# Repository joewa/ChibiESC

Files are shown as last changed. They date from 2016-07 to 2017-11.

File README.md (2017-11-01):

# ChibiESC

Free electric speed controller software using ChibiOS




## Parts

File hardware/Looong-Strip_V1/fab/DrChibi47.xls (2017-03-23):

Source: | /home/joerg/repos/OpenBLDC/joewa/ChibiESC/hardware/Looong-Strip_V1/DrChibi.sch
Date: | Mi 22 Mär 2017 17:17:58 CET
Tool: | Eeschema no-vcs-found-996cba7~58~ubuntu16.04.1
Generator: | /home/joerg/kicad/bom-in-python/bom_csv_grouped_by_value.py
Component Count: | 187
Individual Components:
Item | Qty | Reference(s) | Value | LibPart | Footprint | Datasheet | Comment | Manufacturer | Part Number
 |  | C1 | STM32F4:2.2u / STM32F7:4.7u | BLDC_4-rescue:C-RESCUE-BLDC_4 | Capacitors_SMD:C_0603
 |  | C2 | STM32F4:2.2u / STM32F7:0R | BLDC_4-rescue:C-RESCUE-BLDC_4 | Capacitors_SMD:C_0603
 |  | C3 | 2.2u | BLDC_4-rescue:C-RESCUE-BLDC_4 | Capacitors_SMD:C_0603
 |  | C4 | 2.2u | BLDC_4-rescue:C-RESCUE-BLDC_4 | Capacitors_SMD:C_0603
 |  | C5 | 100n | BLDC_4-rescue:C-RESCUE-BLDC_4 | Capacitors_SMD:C_0603
 |  | CDrGate1 | 0.47uF | device:C | Capacitors_SMD:C_0603_HandSoldering |  | X7R, >10V
 |  | CDrGate2 | 0.47uF | device:C | Capacitors_SMD:C_0603_HandSoldering |  | X7R, >10V
 |  | CDrGate3 | 0.47uF | device:C | Capacitors_SMD:C_0603_HandSoldering |  | X7R, >10V
 |  | CDrGate4 | 0.47uF | device:C | Capacitors_SMD:C_0603_HandSoldering |  | X7R, >10V
 |  | CDrGate5 | 0.47uF | device:C | Capacitors_SMD:C_0603_HandSoldering |  | X7R, >10V
 |  | CDrGate6 | 0.47uF | device:C | Capacitors_SMD:C_0603_HandSoldering |  | X7R, >10V
 |  | CDrHV1 | 10u,35V | device:C | Capacitors_SMD:C_1206 |  | dc link, X7R, >35V
 |  | CDrHV2 | 10u,35V | device:C | Capacitors_SMD:C_1206 |  | dc link, X7R, >35V
 |  | CDrHV3 | 10u,35V | device:C | Capacitors_SMD:C_1206 |  | dc link, X7R, >35V
 |  | CDrHV4 | 10u,35V | device:C | Capacitors_SMD:C_1206 |  | dc link, X7R, >35V
 |  | CDrHV5 | 10u,35V | device:C | Capacitors_SMD:C_1206 |  | dc link, X7R, >35V
 |  | CDrHV6 | 10u,35V | device:C | Capacitors_SMD:C_1206 |  | dc link, X7R, >35V
 |  | CDrHVX1 | C | device:C | Capacitors_SMD:C_1206
 |  | CDrHVX2 | C | device:C | Capacitors_SMD:C_1206
 |  | CDrHVX3 | C | device:C | Capacitors_SMD:C_1206
 |  | CDrHVX4 | C | device:C | Capacitors_SMD:C_1206
 |  | CDrHVX5 | C | device:C | Capacitors_SMD:C_1206
 |  | CDrHVX6 | C | device:C | Capacitors_SMD:C_1206
 |  | CDrHV1back1 | 4.7u,35V | device:C | Capacitors_SMD:C_1206 |  | dc link, X7R, >35V
 |  | CDrHV1back2 | 4.7u,35V | device:C | Capacitors_SMD:C_1206 |  | dc link, X7R, >35V
 |  | CDrHV1back3 | 4.7u,35V | device:C | Capacitors_SMD:C_1206 |  | dc link, X7R, >35V
 |  | CDrHV1back4 | 4.7u,35V | device:C | Capacitors_SMD:C_1206 |  | dc link, X7R, >35V
 |  | CDrHV1back5 | 4.7u,35V | device:C | Capacitors_SMD:C_1206 |  | dc link, X7R, >35V
 |  | CDrHV1back6 | 4.7u,35V | device:C | Capacitors_SMD:C_1206 |  | dc link, X7R, >35V
 |  | CDrHV2back1 | 10u,35V | device:C | Capacitors_SMD:C_1206_HandSoldering |  | dc link, X5R, >35V
 |  | CDrHV2back2 | 10u,35V | device:C | Capacitors_SMD:C_1206_HandSoldering |  | dc link, X5R, >35V
 |  | CDrHV2back3 | 10u,35V | device:C | Capacitors_SMD:C_1206_HandSoldering |  | dc link, X5R, >35V
 |  | CDrHV2back4 | 10u,35V | device:C | Capacitors_SMD:C_1206_HandSoldering |  | dc link, X5R, >35V
 |  | CDrHV2back5 | 10u,35V | device:C | Capacitors_SMD:C_1206_HandSoldering |  | dc link, X5R, >35V
 |  | CDrHV2back6 | 10u,35V | device:C | Capacitors_SMD:C_1206_HandSoldering |  | dc link, X5R, >35V
 |  | CDrHVs1 | 0.47u,35V | device:C | Capacitors_SMD:C_0603 |  | dc link, X7R, >35V
 |  | CDrHVs2 | 0.47u,35V | device:C | Capacitors_SMD:C_0603 |  | dc link, X7R, >35V
 |  | CDrHVs3 | 0.47u,35V | device:C | Capacitors_SMD:C_0603 |  | dc link, X7R, >35V
 |  | CDrHVs4 | 0.47u,35V | device:C | Capacitors_SMD:C_0603 |  | dc link, X7R, >35V
 |  | CDrHVs5 | 0.47u,35V | device:C | Capacitors_SMD:C_0603 |  | dc link, X7R, >35V
 |  | CDrHVs6 | 0.47u,35V | device:C | Capacitors_SMD:C_0603 |  | dc link, X7R, >35V
 |  | CDrLogic1 | 2.2uF | device:C | Capacitors_SMD:C_0603 |  | X7R, >10V | Kemet | C0603C225K8RACTU
 |  | CDrLogic2 | 2.2uF | device:C | Capacitors_SMD:C_0603 |  | X7R, >10V | Kemet | C0603C225K8RACTU
 |  | CDrLogic3 | 2.2uF | device:C | Capacitors_SMD:C_0603 |  | X7R, >10V | Kemet | C0603C225K8RACTU
 |  | CDrLogic4 | 2.2uF | device:C | Capacitors_SMD:C_0603 |  | X7R, >10V | Kemet | C0603C225K8RACTU
 |  | CDrLogic5 | 2.2uF | device:C | Capacitors_SMD:C_0603 |  | X7R, >10V | Kemet | C0603C225K8RACTU
 |  | CDrLogic6 | 2.2uF | device:C | Capacitors_SMD:C_0603 |  | X7R, >10V | Kemet | C0603C225K8RACTU
 |  | CHFAC1 | 10n,35V | device:C | Capacitors_SMD:C_0603_HandSoldering |  | Use COG or NPO ceramic. Or poly- propylene or carbonate
 |  | CONN2 | CONN_01X05 | conn:CONN_01X05 | Pads:Pin_Header_Straight_1x05_Pitch1.27mm
 |  | Cboot1 | 0.47uF | device:C | Capacitors_SMD:C_0603_HandSoldering
 |  | Cboot2 | 0.47uF | device:C | Capacitors_SMD:C_0603_HandSoldering
 |  | Cboot3 | 0.47uF | device:C | Capacitors_SMD:C_0603_HandSoldering
 |  | Cboot4 | 0.47uF | device:C | Capacitors_SMD:C_0603_HandSoldering
 |  | Cboot5 | 0.47uF | device:C | Capacitors_SMD:C_0603_HandSoldering
 |  | Cboot6 | 0.47uF | device:C | Capacitors_SMD:C_0603_HandSoldering
 |  | Ccan1 | 2.2u | BLDC_4-rescue:C-RESCUE-BLDC_4 | Capacitors_SMD:C_0603
 |  | Ccan2 | 2.2u | device:C | Capacitors_SMD:C_0603_HandSoldering
 |  | Ccfilt1 | 0.47n | device:C | Capacitors_SMD:C_0402 |  | Use COG or NPO ceramic. Or poly- propylene or carbonate
 |  | Ccfilt2 | 0.47n | device:C | Capacitors_SMD:C_0402 |  | Use COG or NPO ceramic. Or poly- propylene or carbonate
 |  | Ccfilt3 | 0.47n | device:C | Capacitors_SMD:C_0402 |  | Use COG or NPO ceramic. Or poly- propylene or carbonate
 |  | Ccfilt4 | 0.47n | device:C | Capacitors_SMD:C_0402 |  | Use COG or NPO ceramic. Or poly- propylene or carbonate
 |  | Ccfilt5 | 0.47n | device:C | Capacitors_SMD:C_0402 |  | Use COG or NPO ceramic. Or poly- propylene or carbonate
 |  | Ccfilt6 | 0.47n | device:C | Capacitors_SMD:C_0402 |  | Use COG or NPO ceramic. Or poly- propylene or carbonate
 |  | Cclk1 | 18p | BLDC_4-rescue:C-RESCUE-BLDC_4 | Capacitors_SMD:C_0402 |  | for the crystal
 |  | Cclk2 | 18p | BLDC_4-rescue:C-RESCUE-BLDC_4 | Capacitors_SMD:C_0402 |  | for the crystal
 |  | Cmcu1 | 2.2u | BLDC_4-rescue:C-RESCUE-BLDC_4 | Capacitors_SMD:C_0603
 |  | Cmcu2 | 2.2u | BLDC_4-rescue:C-RESCUE-BLDC_4 | Capacitors_SMD:C_0603
 |  | Cmcu3 | 2.2u | BLDC_4-rescue:C-RESCUE-BLDC_4 | Capacitors_SMD:C_0603
 |  | Cmcu4 | 2.2u | BLDC_4-rescue:C-RESCUE-BLDC_4 | Capacitors_SMD:C_0603
 |  | Cpwr1 | 4.7u,35V | BLDC_4-rescue:C-RESCUE-BLDC_4 | Capacitors_SMD:C_0805 |  | X7R, e.g. GRM32ER7YA106KA12L
 |  | Cpwr2 | 10u,35V | BLDC_4-rescue:C-RESCUE-BLDC_4 | Capacitors_SMD:C_2220
 |  | Csens1 | 0.47u | device:C | Capacitors_SMD:C_0603 |  | bypass capacitor for ACS711, X7R, >10V
 |  | Csens2 | 0.47u | device:C | Capacitors_SMD:C_0603 |  | bypass capacitor for ACS711, X7R, >10V
 |  | Csens3 | 0.47u | device:C | Capacitors_SMD:C_0603 |  | bypass capacitor for ACS711, X7R, >10V
 |  | Csens4 | 0.47u | device:C | Capacitors_SMD:C_0603 |  | bypass capacitor for ACS711, X7R, >10V
 |  | Csens5 | 0.47u | device:C | Capacitors_SMD:C_0603 |  | bypass capacitor for ACS711, X7R, >10V
 |  | Csens6 | 0.47u | device:C | Capacitors_SMD:C_0603 |  | bypass capacitor for ACS711, X7R, >10V
 |  | C3vi1 | 100u | BLDC_4-rescue:CP1-RESCUE-BLDC_4 | Capacitors_SMD:C_0805
 |  | C3vi2 | 1u | device:C | Capacitors_SMD:C_0603
 |  | C3vn1 | 10n | device:C | Capacitors_SMD:C_0603 |  | Use COG or NPO ceramic. Or poly- propylene or carbonate
 |  | C3vo1 | 4.7u | BLDC_4-rescue:CP1-RESCUE-BLDC_4 | Capacitors_SMD:C_0805
 |  | C5vo1 | 2.2u | BLDC_4-rescue:C-RESCUE-BLDC_4 | Capacitors_SMD:C_0603
 |  | C5vo2 | 100u | BLDC_4-rescue:CP1-RESCUE-BLDC_4 | Capacitors_SMD:C_0805
 |  | D1 | RED | BLDC_4-rescue:LED-RESCUE-BLDC_4 | LEDs:LED_0402
 |  | D2 | GREEN | BLDC_4-rescue:LED-RESCUE-BLDC_4 | LEDs:LED_0402
 |  | Dclamp1 | D_Schottky_x2_Serial_AKC__BAT754S | device:D_Schottky_x2_Serial_AKC | TO_SOT_Packages_SMD:SOT-23 |  |  | NXP | BAT754S
 |  | Dusb1 | BAT46WH | DrChibi-cache:BAT46WH | Diodes_SMD:SOD-123 |  |  | NXP | BAT46WH
 |  | JP1 | STM32F4:0R / STM32F7:DNP | device:R | Capacitors_SMD:C_0402
 |  | JP2 | STM32F4:0R / STM32F7:DNP | device:R | Capacitors_SMD:C_0402
 |  | JP3 | STM32F4:DNP / STM32F7:0R | device:R | Capacitors_SMD:C_0402
 |  | JP4 | STM32F4:0R / STM32F7:DNP | device:R | Capacitors_SMD:C_0402
 |  | JP5 | STM32F4:DNP / STM32F7:0R | device:R | Capacitors_SMD:C_0402
 |  | JP6 | STM32F4:0R / STM32F7:DNP | device:R | Capacitors_SMD:C_0402
 |  | JP8 | STM32F4:DNP / STM32F7:0R | device:R | Capacitors_SMD:C_0402
 |  | JP9 | STM32F4:0R / STM32F7:DNP | device:R | Capacitors_SMD:C_0402
 |  | JP10 | STM32F4:DNP / STM32F7:0R | device:R | Capacitors_SMD:C_0402
 |  | JP12 | STM32F4:DNP / STM32F7:0R | device:R | Capacitors_SMD:C_0402
 |  | JP13 | STM32F4:DNP / STM32F7:0R | device:R | Capacitors_SMD:C_0402
 |  | P1 | CONN_02X05 | conn:CONN_02X05 | Pads:Pin_Header_Straight_2x05_Pitch1.27mm
 |  | P3 | IN+ | DrChibi-cache:CONN_1 | Pads:1PAD_3x6mm
 |  | P4 | IN- | DrChibi-cache:CONN_1 | Pads:1PAD_3.5x6mm
 |  | P5 | CONN_01X04 | conn:CONN_01X04 | Connectors_Molex:Connector_Molex_PicoBlade_53261-0471 |  |  | Molex | PicoBlade 53261-0471
 |  | PBOOT1GND1 | PAD_SMD | pkl_misc:PAD_SMD | Pads:PAD_SMD_1x1
 |  | PBOOT0P1 | PAD_SMD | pkl_misc:PAD_SMD | Pads:PAD_SMD_1x1
 |  | PBOOT1P1 | PAD_SMD | pkl_misc:PAD_SMD | Pads:PAD_SMD_1x1
 |  | PBOOT03V31 | PAD_SMD | pkl_misc:PAD_SMD | Pads:PAD_SMD_1x1
 |  | PHFAC1 | PAD_SMD | pkl_misc:PAD_SMD | Pads:PAD_SMD_1.2x2.5
 |  | PMotor1 | PAD_SMD | pkl_misc:PAD_SMD | CRF1:1PAD_4x5mm
 |  | PMotor2 | PAD_SMD | pkl_misc:PAD_SMD | CRF1:1PAD_4x5mm
 |  | PMotor3 | PAD_SMD | pkl_misc:PAD_SMD | CRF1:1PAD_4x5mm
 |  | PMotor4 | PAD_SMD | pkl_misc:PAD_SMD | CRF1:1PAD_4x5mm
 |  | PMotor5 | PAD_SMD | pkl_misc:PAD_SMD | CRF1:1PAD_4x5mm
 |  | PMotor6 | PAD_SMD | pkl_misc:PAD_SMD | CRF1:1PAD_4x5mm
 |  | PVSens1 | PAD_SMD | pkl_misc:PAD_SMD | Pads:PAD_SMD_1x1
 |  | PVSens2 | PAD_SMD | pkl_misc:PAD_SMD | Pads:PAD_SMD_1x1
 |  | PVSens3 | PAD_SMD | pkl_misc:PAD_SMD | Pads:PAD_SMD_1x1
 |  | PVSens4 | PAD_SMD | pkl_misc:PAD_SMD | Pads:PAD_SMD_1x1
 |  | PVSens5 | PAD_SMD | pkl_misc:PAD_SMD | Pads:PAD_SMD_1x1
 |  | PVSens6 | PAD_SMD | pkl_misc:PAD_SMD | Pads:PAD_SMD_1x1
 |  | P_PWM2 | PAD_SMD | pkl_misc:PAD_SMD | Pads:PAD_SMD_1x1
 |  | P_PWM3 | PAD_SMD | pkl_misc:PAD_SMD | Pads:PAD_SMD_1x1
 |  | P_PWM4 | PAD_SMD | pkl_misc:PAD_SMD | Pads:PAD_SMD_1x1
 |  | R1 | 100R | device:R | Resistors_SMD:R_0603
 |  | R2 | 100R | device:R | Resistors_SMD:R_0603
 |  | R3 | 2k2 | device:R | Resistors_SMD:R_0402
 |  | R4 | 0R | device:R | Resistors_SMD:R_0805
 |  | RDrLogic1 | 100R | device:R | Resistors_SMD:R_0603
 |  | RDrLogic2 | 100R | device:R | Resistors_SMD:R_0603
 |  | RDrLogic3 | 100R | device:R | Resistors_SMD:R_0603
 |  | RDrLogic4 | 100R | device:R | Resistors_SMD:R_0603
 |  | RDrLogic5 | 100R | device:R | Resistors_SMD:R_0603
 |  | RDrLogic6 | 100R | device:R | Resistors_SMD:R_0603
 |  | RHFAC1 | 100R | device:R | Resistors_SMD:R_0603_HandSoldering
 |  | RY1 | R/DNP | device:R | Resistors_SMD:R_0603_HandSoldering
 |  | RY2 | R/DNP | device:R | Resistors_SMD:R_0603_HandSoldering
 |  | RY3 | R/DNP | device:R | Resistors_SMD:R_0603_HandSoldering
 |  | RY4 | R/DNP | device:R | Resistors_SMD:R_0603_HandSoldering
 |  | RY5 | R/DNP | device:R | Resistors_SMD:R_0603_HandSoldering
 |  | RY6 | R/DNP | device:R | Resistors_SMD:R_0603_HandSoldering
 |  | RYOFFS1 | 20k | device:R | Resistors_SMD:R_0603_HandSoldering
 |  | RYS1 | 0R/DNP | device:R | Resistors_SMD:R_0603_HandSoldering
 |  | RYSGND1 | 20k | device:R | Resistors_SMD:R_0402
 |  | Radj1 | 165R | device:R | Resistors_SMD:R_0402
 |  | Rcan1 | NI | BLDC_4-rescue:R-RESCUE-BLDC_4 | Resistors_SMD:R_0603_HandSoldering
 |  | Rcfilt1 | 20k | device:R | Resistors_SMD:R_0402
 |  | Rcfilt2 | 20k | device:R | Resistors_SMD:R_0402
 |  | Rcfilt3 | 20k | device:R | Resistors_SMD:R_0402
 |  | Rcfilt4 | 20k | device:R | Resistors_SMD:R_0402
 |  | Rcfilt5 | 20k | device:R | Resistors_SMD:R_0402
 |  | Rcfilt6 | 20k | device:R | Resistors_SMD:R_0402
 |  | Rhsens1 | 10k,0.1% | device:R | Capacitors_SMD:C_0603_HandSoldering
 |  | Rhsens2 | 10k,0.1% | device:R | Capacitors_SMD:C_0603_HandSoldering
 |  | Rhsens3 | 10k,0.1% | device:R | Capacitors_SMD:C_0603_HandSoldering
 |  | Rhsens4 | 10k,0.1% | device:R | Capacitors_SMD:C_0603_HandSoldering
 |  | Rhsens5 | 10k,0.1% | device:R | Capacitors_SMD:C_0603_HandSoldering
 |  | Rhsens6 | 10k,0.1% | device:R | Capacitors_SMD:C_0603_HandSoldering
 |  | Rled1 | 100R | BLDC_4-rescue:R-RESCUE-BLDC_4 | Resistors_SMD:R_0402
 |  | Rled2 | 100R | BLDC_4-rescue:R-RESCUE-BLDC_4 | Resistors_SMD:R_0402
 |  | Rlsens1 | 2k2,0.1% | device:R | Resistors_SMD:R_0402
 |  | Rlsens2 | 2k2,0.1% | device:R | Resistors_SMD:R_0402
 |  | Rlsens3 | 2k2,0.1% | device:R | Resistors_SMD:R_0402
 |  | Rlsens4 | 2k2,0.1% | device:R | Resistors_SMD:R_0402
 |  | Rlsens5 | 2k2,0.1% | device:R | Resistors_SMD:R_0402
 |  | Rlsens6 | 2k2,0.1% | device:R | Resistors_SMD:R_0402
 |  | Rthwn1 | 2k2 | device:R | Resistors_SMD:R_0402
 |  | Rusb1 | 10k | device:R | Resistors_SMD:R_0402
 |  | Rusb2 | 22R | BLDC_4-rescue:R-RESCUE-BLDC_4 | Resistors_SMD:R_0402
 |  | Rusb3 | 22R | BLDC_4-rescue:R-RESCUE-BLDC_4 | Resistors_SMD:R_0402
 |  | R3vi1 | 2R7 | device:R | Resistors_SMD:R_0805 |  | Filter resistor to Has to dissipate 1/4W.
 |  | U1 | STM32F40X_LQFP64 | crf_1:STM32F40X_LQFP64 | CRF1:lqfp64_pad_mod |  |  | ST | STM32F405RGTx
 |  | U2 | ISO1050 | crf_1:ISO1050 | CRF1:PDSO-G8
 |  | UDrmos1 | DrMOS_SiC632A | pkl_drmos:DrMOS_SiC632A | DrMOS:MLP55-31L | http://www.vishay.com/docs/62992/sic632a.pdf |  | Vishay | SiC632ACD-T1-GE3
 |  | UDrmos2 | DrMOS_SiC632A | pkl_drmos:DrMOS_SiC632A | DrMOS:MLP55-31L | http://www.vishay.com/docs/62992/sic632a.pdf |  | Vishay | SiC632ACD-T1-GE3
 |  | UDrmos3 | DrMOS_SiC632A | pkl_drmos:DrMOS_SiC632A | DrMOS:MLP55-31L | http://www.vishay.com/docs/62992/sic632a.pdf |  | Vishay | SiC632ACD-T1-GE3
 |  | UDrmos4 | DrMOS_SiC632A | pkl_drmos:DrMOS_SiC632A | DrMOS:MLP55-31L | http://www.vishay.com/docs/62992/sic632a.pdf |  | Vishay | SiC632ACD-T1-GE3
 |  | UDrmos5 | DrMOS_SiC632A | pkl_drmos:DrMOS_SiC632A | DrMOS:MLP55-31L | http://www.vishay.com/docs/62992/sic632a.pdf |  | Vishay | SiC632ACD-T1-GE3
 |  | UDrmos6 | DrMOS_SiC632A | pkl_drmos:DrMOS_SiC632A | DrMOS:MLP55-31L | http://www.vishay.com/docs/62992/sic632a.pdf |  | Vishay | SiC632ACD-T1-GE3
 |  | Ureg1 | LTM8020 | pkl_regulator:LTM8020 | Regulators_User:Housings_LGA_21_6.25x6.25mm | http://cds.linear.com/docs/en/datasheet/8020fd.pdf |  | Linear Technology | LTM8020V
 |  | Ureg2 | LP2992AIM5-3.3 | pkl_misc:LP2992AIM5-3.3 | TO_SOT_Packages_SMD:SOT-23-5 | http://www.ti.com/lit/ds/symlink/lp2992.pdf |  | Texas Instruments | LP2992AIM5-3.3/NOPB
 |  | Usens1 | ACS711 | pkl_sensor:ACS711 | Allegro:QFN-12-1EX_3x3mm_Pitch0.5mm |  |  | Allegro | ACS711KEXLT-31AB-T
 |  | Usens2 | ACS711 | pkl_sensor:ACS711 | Allegro:QFN-12-1EX_3x3mm_Pitch0.5mm |  |  | Allegro | ACS711KEXLT-31AB-T
 |  | Usens3 | ACS711 | pkl_sensor:ACS711 | Allegro:QFN-12-1EX_3x3mm_Pitch0.5mm |  |  | Allegro | ACS711KEXLT-31AB-T
 |  | Usens4 | ACS711 | pkl_sensor:ACS711 | Allegro:QFN-12-1EX_3x3mm_Pitch0.5mm |  |  | Allegro | ACS711KEXLT-31AB-T
 |  | Usens5 | ACS711 | pkl_sensor:ACS711 | Allegro:QFN-12-1EX_3x3mm_Pitch0.5mm |  |  | Allegro | ACS711KEXLT-31AB-T
 |  | Usens6 | ACS711 | pkl_sensor:ACS711 | Allegro:QFN-12-1EX_3x3mm_Pitch0.5mm |  |  | Allegro | ACS711KEXLT-31AB-T
 |  | X1 | MINI-USB-SHIELD-32005-201 | crf_1:MINI-USB-SCHIELD-32005-201 | CRF1:mini_USB_gnd |  |  | Cypress Industries | CCMUSBB-32005-201
 |  | X2 | 8MHz 10ppm | DrChibi-rescue:CRYSTAL_SMD-RESCUE-DrChibi | Crystals_User:Crystal_5x3mm |  |  |  | ABM3B-8.0-10-1UT
Collated Components:
Item | Qty | Reference(s) | Value | LibPart | Footprint | Datasheet | Comment | Manufacturer | Part Number
1 | 1 | C1 | STM32F4:2.2u / STM32F7:4.7u | BLDC_4-rescue:C-RESCUE-BLDC_4 | Capacitors_SMD:C_0603
2 | 1 | C2 | STM32F4:2.2u / STM32F7:0R | BLDC_4-rescue:C-RESCUE-BLDC_4 | Capacitors_SMD:C_0603
3 | 8 | C3, C4, Ccan1, Cmcu1, Cmcu2, Cmcu3, Cmcu4, C5vo1 | 2.2u | BLDC_4-rescue:C-RESCUE-BLDC_4 | Capacitors_SMD:C_0603
4 | 1 | C5 | 100n | BLDC_4-rescue:C-RESCUE-BLDC_4 | Capacitors_SMD:C_0603
5 | 12 | CDrGate1, CDrGate2, CDrGate3, CDrGate4, CDrGate5, CDrGate6, Cboot1, Cboot2, Cboot3, Cboot4, Cboot5, Cboot6 | 0.47uF | device:C | Capacitors_SMD:C_0603_HandSoldering |  | X7R, >10V
6 | 6 | CDrHV1, CDrHV2, CDrHV3, CDrHV4, CDrHV5, CDrHV6 | 10u,35V | device:C | Capacitors_SMD:C_1206 |  | dc link, X7R, >35V
7 | 6 | CDrHVX1, CDrHVX2, CDrHVX3, CDrHVX4, CDrHVX5, CDrHVX6 | C | device:C | Capacitors_SMD:C_1206
8 | 6 | CDrHV1back1, CDrHV1back2, CDrHV1back3, CDrHV1back4, CDrHV1back5, CDrHV1back6 | 4.7u,35V | device:C | Capacitors_SMD:C_1206 |  | dc link, X7R, >35V
9 | 6 | CDrHV2back1, CDrHV2back2, CDrHV2back3, CDrHV2back4, CDrHV2back5, CDrHV2back6 | 10u,35V | device:C | Capacitors_SMD:C_1206_HandSoldering |  | dc link, X5R, >35V
10 | 6 | CDrHVs1, CDrHVs2, CDrHVs3, CDrHVs4, CDrHVs5, CDrHVs6 | 0.47u,35V | device:C | Capacitors_SMD:C_0603 |  | dc link, X7R, >35V
11 | 6 | CDrLogic1, CDrLogic2, CDrLogic3, CDrLogic4, CDrLogic5, CDrLogic6 | 2.2uF | device:C | Capacitors_SMD:C_0603 |  | X7R, >10V | Kemet | C0603C225K8RACTU
12 | 1 | CHFAC1 | 10n,35V | device:C | Capacitors_SMD:C_0603_HandSoldering |  | Use COG or NPO ceramic. Or poly- propylene or carbonate
13 | 1 | CONN2 | CONN_01X05 | conn:CONN_01X05 | Pads:Pin_Header_Straight_1x05_Pitch1.27mm
14 | 1 | Ccan2 | 2.2u | device:C | Capacitors_SMD:C_0603_HandSoldering
15 | 6 | Ccfilt1, Ccfilt2, Ccfilt3, Ccfilt4, Ccfilt5, Ccfilt6 | 0.47n | device:C | Capacitors_SMD:C_0402 |  | Use COG or NPO ceramic. Or poly- propylene or carbonate
16 | 2 | Cclk1, Cclk2 | 18p | BLDC_4-rescue:C-RESCUE-BLDC_4 | Capacitors_SMD:C_0402 |  | for the crystal
17 | 1 | Cpwr1 | 4.7u,35V | BLDC_4-rescue:C-RESCUE-BLDC_4 | Capacitors_SMD:C_0805 |  | X7R, e.g. GRM32ER7YA106KA12L
18 | 1 | Cpwr2 | 10u,35V | BLDC_4-rescue:C-RESCUE-BLDC_4 | Capacitors_SMD:C_2220
19 | 6 | Csens1, Csens2, Csens3, Csens4, Csens5, Csens6 | 0.47u | device:C | Capacitors_SMD:C_0603 |  | bypass capacitor for ACS711, X7R, >10V
20 | 2 | C3vi1, C5vo2 | 100u | BLDC_4-rescue:CP1-RESCUE-BLDC_4 | Capacitors_SMD:C_0805
21 | 1 | C3vi2 | 1u | device:C | Capacitors_SMD:C_0603
22 | 1 | C3vn1 | 10n | device:C | Capacitors_SMD:C_0603 |  | Use COG or NPO ceramic. Or poly- propylene or carbonate
23 | 1 | C3vo1 | 4.7u | BLDC_4-rescue:CP1-RESCUE-BLDC_4 | Capacitors_SMD:C_0805
24 | 1 | D1 | RED | BLDC_4-rescue:LED-RESCUE-BLDC_4 | LEDs:LED_0402
25 | 1 | D2 | GREEN | BLDC_4-rescue:LED-RESCUE-BLDC_4 | LEDs:LED_0402
26 | 1 | Dclamp1 | D_Schottky_x2_Serial_AKC__BAT754S | device:D_Schottky_x2_Serial_AKC | TO_SOT_Packages_SMD:SOT-23 |  |  | NXP | BAT754S
27 | 1 | Dusb1 | BAT46WH | DrChibi-cache:BAT46WH | Diodes_SMD:SOD-123 |  |  | NXP | BAT46WH
28 | 5 | JP1, JP2, JP4, JP6, JP9 | STM32F4:0R / STM32F7:DNP | device:R | Capacitors_SMD:C_0402
29 | 6 | JP3, JP5, JP8, JP10, JP12, JP13 | STM32F4:DNP / STM32F7:0R | device:R | Capacitors_SMD:C_0402
30 | 1 | P1 | CONN_02X05 | conn:CONN_02X05 | Pads:Pin_Header_Straight_2x05_Pitch1.27mm
31 | 1 | P3 | IN+ | DrChibi-cache:CONN_1 | Pads:1PAD_3x6mm
32 | 1 | P4 | IN- | DrChibi-cache:CONN_1 | Pads:1PAD_3.5x6mm
33 | 1 | P5 | CONN_01X04 | conn:CONN_01X04 | Connectors_Molex:Connector_Molex_PicoBlade_53261-0471 |  |  | Molex | PicoBlade 53261-0471
34 | 13 | PBOOT1GND1, PBOOT0P1, PBOOT1P1, PBOOT03V31, PVSens1, PVSens2, PVSens3, PVSens4, PVSens5, PVSens6, P_PWM2, P_PWM3, P_PWM4 | PAD_SMD | pkl_misc:PAD_SMD | Pads:PAD_SMD_1x1
35 | 1 | PHFAC1 | PAD_SMD | pkl_misc:PAD_SMD | Pads:PAD_SMD_1.2x2.5
36 | 6 | PMotor1, PMotor2, PMotor3, PMotor4, PMotor5, PMotor6 | PAD_SMD | pkl_misc:PAD_SMD | CRF1:1PAD_4x5mm
37 | 8 | R1, R2, RDrLogic1, RDrLogic2, RDrLogic3, RDrLogic4, RDrLogic5, RDrLogic6 | 100R | device:R | Resistors_SMD:R_0603
38 | 2 | R3, Rthwn1 | 2k2 | device:R | Resistors_SMD:R_0402
39 | 1 | R4 | 0R | device:R | Resistors_SMD:R_0805
40 | 1 | RHFAC1 | 100R | device:R | Resistors_SMD:R_0603_HandSoldering
41 | 6 | RY1, RY2, RY3, RY4, RY5, RY6 | R/DNP | device:R | Resistors_SMD:R_0603_HandSoldering
42 | 1 | RYOFFS1 | 20k | device:R | Resistors_SMD:R_0603_HandSoldering
43 | 1 | RYS1 | 0R/DNP | device:R | Resistors_SMD:R_0603_HandSoldering
44 | 7 | RYSGND1, Rcfilt1, Rcfilt2, Rcfilt3, Rcfilt4, Rcfilt5, Rcfilt6 | 20k | device:R | Resistors_SMD:R_0402
45 | 1 | Radj1 | 165R | device:R | Resistors_SMD:R_0402
46 | 1 | Rcan1 | NI | BLDC_4-rescue:R-RESCUE-BLDC_4 | Resistors_SMD:R_0603_HandSoldering
47 | 6 | Rhsens1, Rhsens2, Rhsens3, Rhsens4, Rhsens5, Rhsens6 | 10k,0.1% | device:R | Capacitors_SMD:C_0603_HandSoldering
48 | 2 | Rled1, Rled2 | 100R | BLDC_4-rescue:R-RESCUE-BLDC_4 | Resistors_SMD:R_0402
49 | 6 | Rlsens1, Rlsens2, Rlsens3, Rlsens4, Rlsens5, Rlsens6 | 2k2,0.1% | device:R | Resistors_SMD:R_0402
50 | 1 | Rusb1 | 10k | device:R | Resistors_SMD:R_0402
51 | 2 | Rusb2, Rusb3 | 22R | BLDC_4-rescue:R-RESCUE-BLDC_4 | Resistors_SMD:R_0402
52 | 1 | R3vi1 | 2R7 | device:R | Resistors_SMD:R_0805 |  | Filter resistor to Has to dissipate 1/4W.
53 | 1 | U1 | STM32F40X_LQFP64 | crf_1:STM32F40X_LQFP64 | CRF1:lqfp64_pad_mod |  |  | ST | STM32F4: STM32F405RGTx / STM32F7: STM32F722RE
54 | 1 | U2 | ISO1050 | crf_1:ISO1050 | CRF1:PDSO-G8
55 | 6 | UDrmos1, UDrmos2, UDrmos3, UDrmos4, UDrmos5, UDrmos6 | DrMOS_SiC632A | pkl_drmos:DrMOS_SiC632A | DrMOS:MLP55-31L | http://www.vishay.com/docs/62992/sic632a.pdf |  | Vishay | SiC632ACD-T1-GE3
56 | 1 | Ureg1 | LTM8020 | pkl_regulator:LTM8020 | Regulators_User:Housings_LGA_21_6.25x6.25mm | http://cds.linear.com/docs/en/datasheet/8020fd.pdf |  | Linear Technology | LTM8020V
57 | 1 | Ureg2 | LP2992AIM5-3.3 | pkl_misc:LP2992AIM5-3.3 | TO_SOT_Packages_SMD:SOT-23-5 | http://www.ti.com/lit/ds/symlink/lp2992.pdf |  | Texas Instruments | LP2992AIM5-3.3/NOPB
58 | 6 | Usens1, Usens2, Usens3, Usens4, Usens5, Usens6 | ACS711 | pkl_sensor:ACS711 | Allegro:QFN-12-1EX_3x3mm_Pitch0.5mm |  |  | Allegro | ACS711KEXLT-31AB-T
59 | 1 | X1 | MINI-USB-SHIELD-32005-201 | crf_1:MINI-USB-SCHIELD-32005-201 | CRF1:mini_USB_gnd |  |  | Cypress Industries | CCMUSBB-32005-201
60 | 1 | X2 | 8MHz 10ppm | DrChibi-rescue:CRYSTAL_SMD-RESCUE-DrChibi | Crystals_User:Crystal_5x3mm |  |  |  | ABM3B-8.0-10-1UT

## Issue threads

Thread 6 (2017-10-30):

Problems with pulse pattern generation when at least two phases have the same duty cycle.

joewa, 2017-10-30:
**This test case fails:**
OK svm30.du = 0.750000000
OK svm30.dw = 0.250000000
OK svm30.dv = 0.250000000
OK svm30.mode = 1.000000000
OK pwm3dma0.enable = 1.000000000

**This test case is OK:**
OK svm30.du = 0.750000000
OK svm30.dv = 0.250000000
OK svm30.dw = 0.500000000
OK svm30.mode = 1.000000000
OK pwm3dma0.enable = 1.000000000

joewa, 2017-10-30:
This test case is OK too:
OK svm30.du = 0.250000000
OK svm30.dv = 0.250000000
OK svm30.dw = 0.750000000
OK svm30.mode = 1.000000000
OK pwm3dma0.enable = 1.000000000

The problem might occur only, when at least the last 2 phases have the same duty cycle

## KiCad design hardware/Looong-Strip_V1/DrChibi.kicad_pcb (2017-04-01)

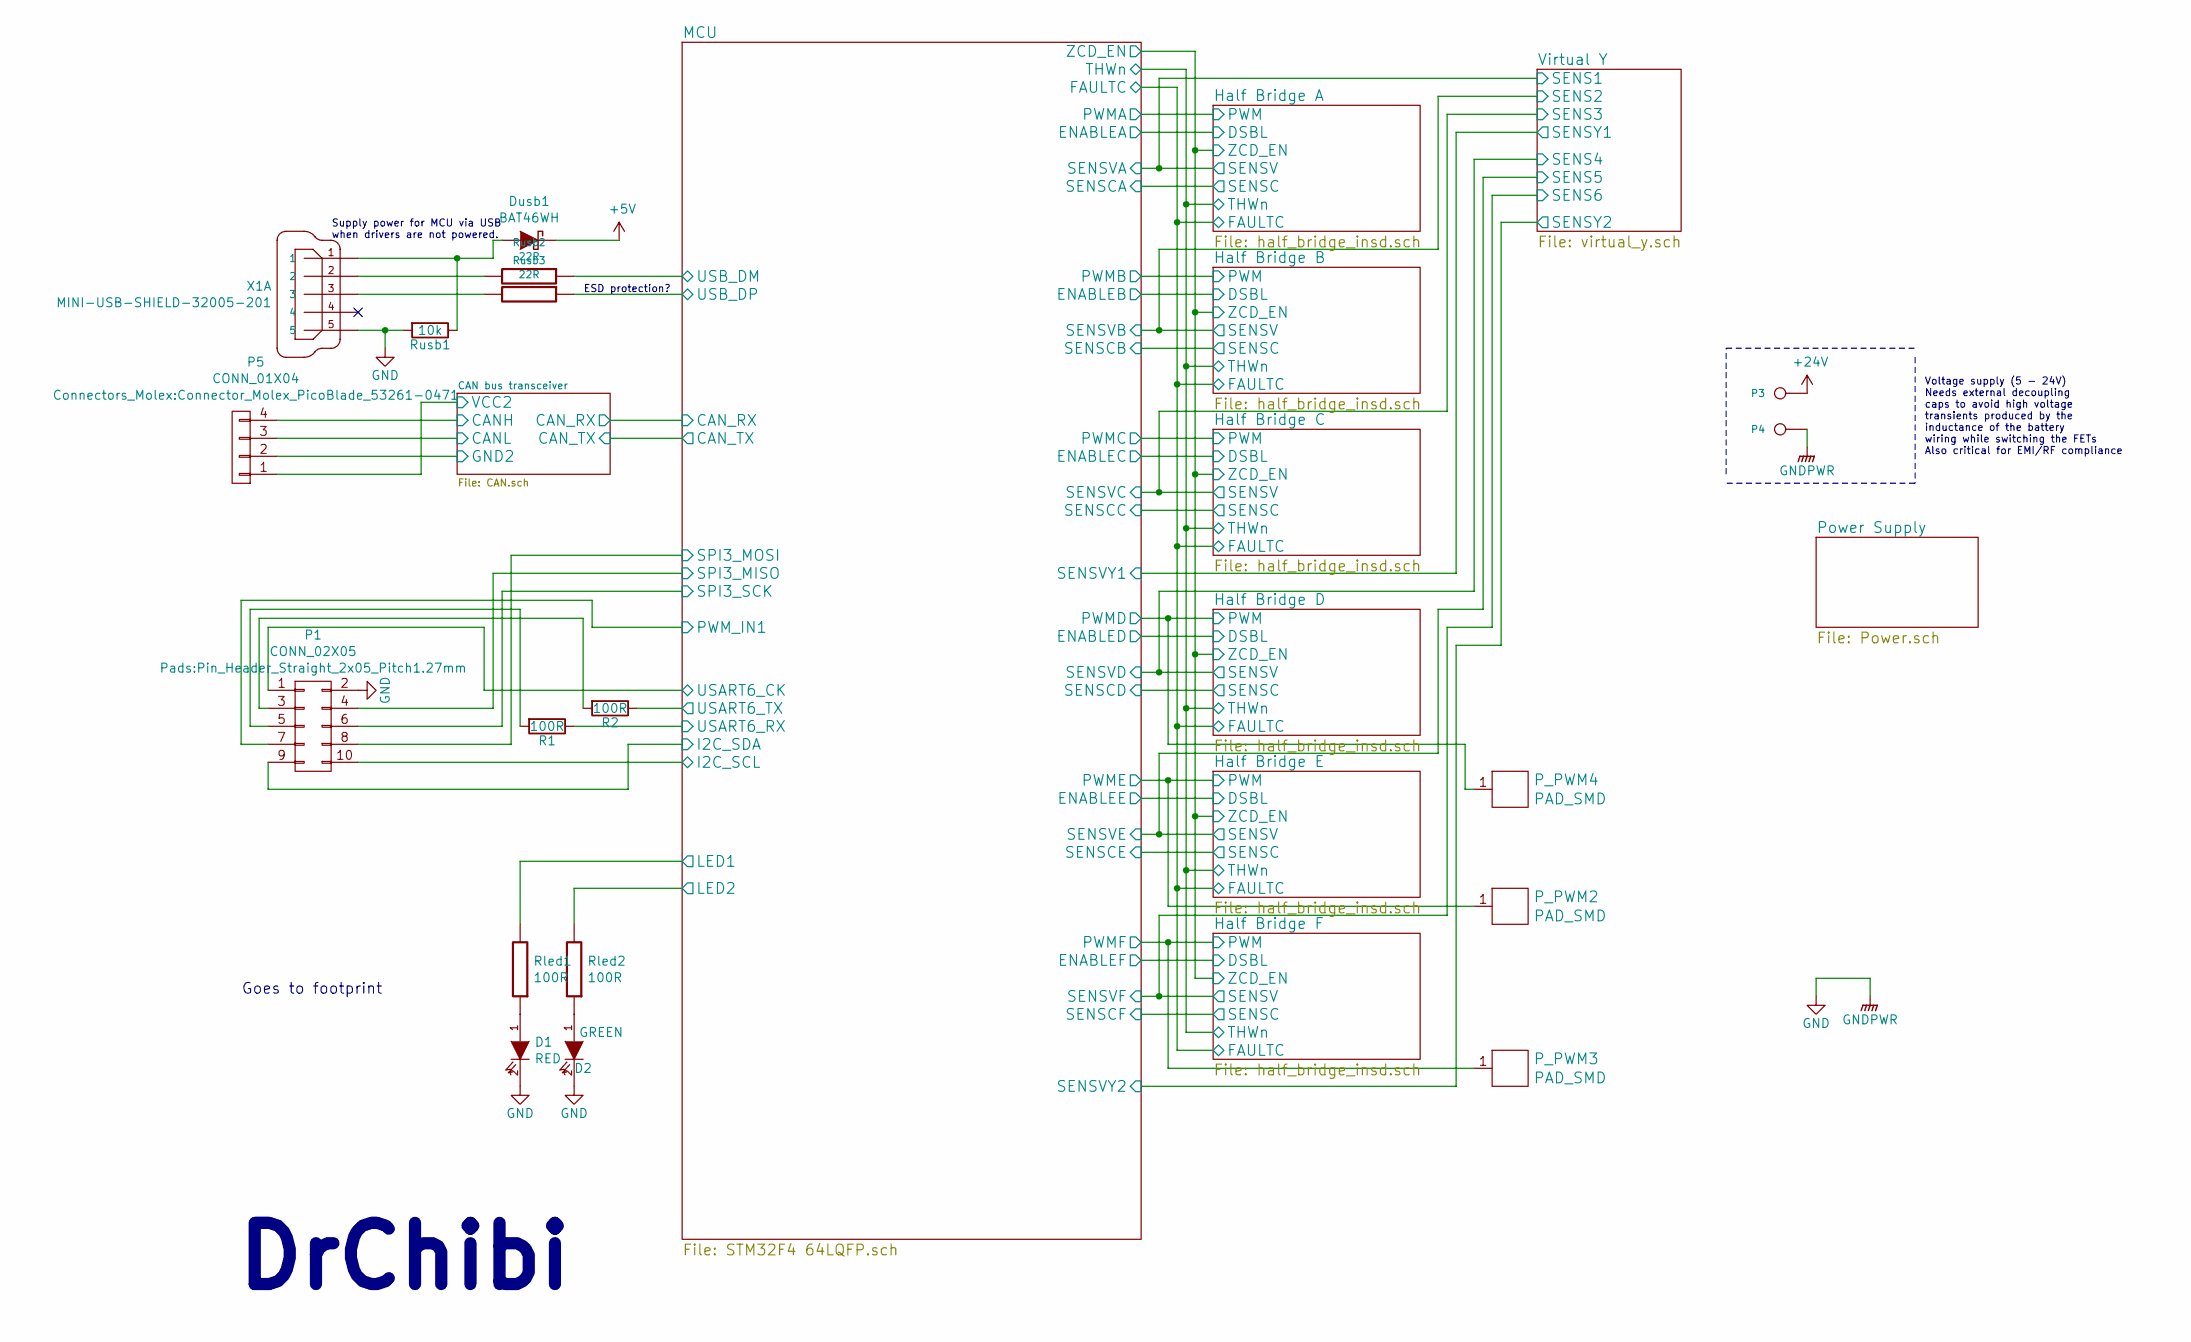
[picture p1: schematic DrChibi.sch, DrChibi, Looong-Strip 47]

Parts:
D1: RED; LED_0402
D2: GREEN; LED_0402
Dusb1: BAT46WH; SOD-123; Part Number BAT46WH
P1: CONN_02X05; Pin_Header_Straight_2x05_Pitch1.27mm
P3: IN+; 1PAD_3x6mm
P4: IN-; 1PAD_3.5x6mm
P5: CONN_01X04; Connector_Molex_PicoBlade_53261-0471; Part Number PicoBlade 53261-0471
P_PWM2, P_PWM3, P_PWM4: PAD_SMD; PAD_SMD_1x1
R1, R2: 100R; R_0603
Rled1, Rled2: 100R; R_0402
Rusb1: 10k; R_0402
Rusb2, Rusb3: 22R; R_0402
X1: MINI-USB-SHIELD-32005-201; mini_USB_gnd; Part Number CCMUSBB-32005-201

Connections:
+5V: Dusb1.1 (K); also elsewhere on the board
+24V: P3.1; also elsewhere on the board
/CAN bus transceiver/CANH: P5.4; also elsewhere on the board
/CAN bus transceiver/CANL: P5.3; also elsewhere on the board
/CAN bus transceiver/GND2: P5.2; also elsewhere on the board
/CAN bus transceiver/VCC2: P5.1; also elsewhere on the board
/Half Bridge D/PWM: P_PWM4.1; also elsewhere on the board
/Half Bridge E/PWM: P_PWM2.1; also elsewhere on the board
/Half Bridge F/PWM: P_PWM3.1; also elsewhere on the board
/MCU/I2C_SCL: P1.10; also elsewhere on the board
/MCU/I2C_SDA: P1.9; also elsewhere on the board
/MCU/LED1: Rled1.2; also elsewhere on the board
/MCU/LED2: Rled2.2; also elsewhere on the board
/MCU/PWM_IN1: P1.7; also elsewhere on the board
/MCU/SPI3_MISO: P1.4; also elsewhere on the board
/MCU/SPI3_MOSI: P1.8; also elsewhere on the board
/MCU/SPI3_SCK: P1.6; also elsewhere on the board
/MCU/USART6_CK: P1.1; also elsewhere on the board
/MCU/USART6_RX: R1.1; also elsewhere on the board
/MCU/USART6_TX: R2.1; also elsewhere on the board
/MCU/USB_DM: Rusb2.1; also elsewhere on the board
/MCU/USB_DP: Rusb3.1; also elsewhere on the board
GND: D1.2 (K), D2.2 (K), P1.2, P4.1, Rusb1.2, X1.5; also elsewhere on the board
unnamed: D1.1 (A), Rled1.1
unnamed: D2.1 (A), Rled2.1
unnamed: Dusb1.2 (A), Rusb1.1, X1.1
unnamed: P1.3, R2.2
unnamed: P1.5, R1.2
unnamed: Rusb2.2, X1.2
unnamed: Rusb3.2, X1.3

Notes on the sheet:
Supply power for MCU via USB when drivers are not powered.
ESD protection?
DrChibi
Voltage supply (5 - 24V) Needs external decoupling caps to avoid high voltage transients produced by the inductance of the battery wiring while switching the FETs Also critical for EMI/RF compliance
Goes to footprint

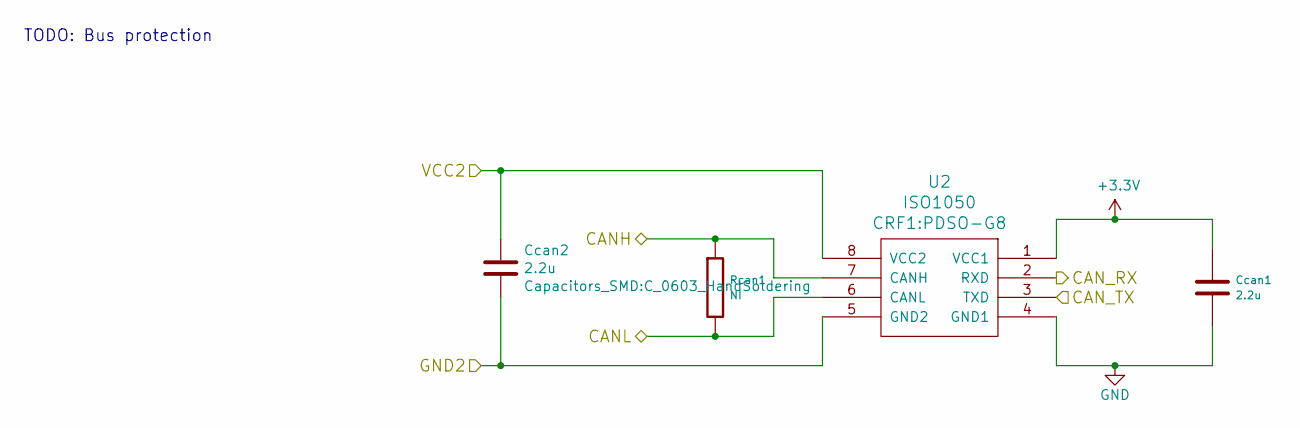
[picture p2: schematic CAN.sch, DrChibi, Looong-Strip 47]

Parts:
Ccan1: 2.2u; C_0603
Ccan2: 2.2u; C_0603_HandSoldering
Rcan1: NI; R_0603_HandSoldering
U2: ISO1050; PDSO-G8

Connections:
+3V3: Ccan1.1, U2.1 (VCC1); also elsewhere on the board
/CAN bus transceiver/CANH: Rcan1.1, U2.7 (CANH); also elsewhere on the board
/CAN bus transceiver/CANL: Rcan1.2, U2.6 (CANL); also elsewhere on the board
/CAN bus transceiver/CAN_RX: U2.2 (RXD); also elsewhere on the board
/CAN bus transceiver/CAN_TX: U2.3 (TXD); also elsewhere on the board
/CAN bus transceiver/GND2: Ccan2.2, U2.5 (GND2); also elsewhere on the board
/CAN bus transceiver/VCC2: Ccan2.1, U2.8 (VCC2); also elsewhere on the board
GND: Ccan1.2, U2.4 (GND1); also elsewhere on the board

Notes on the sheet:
TODO: Bus protection

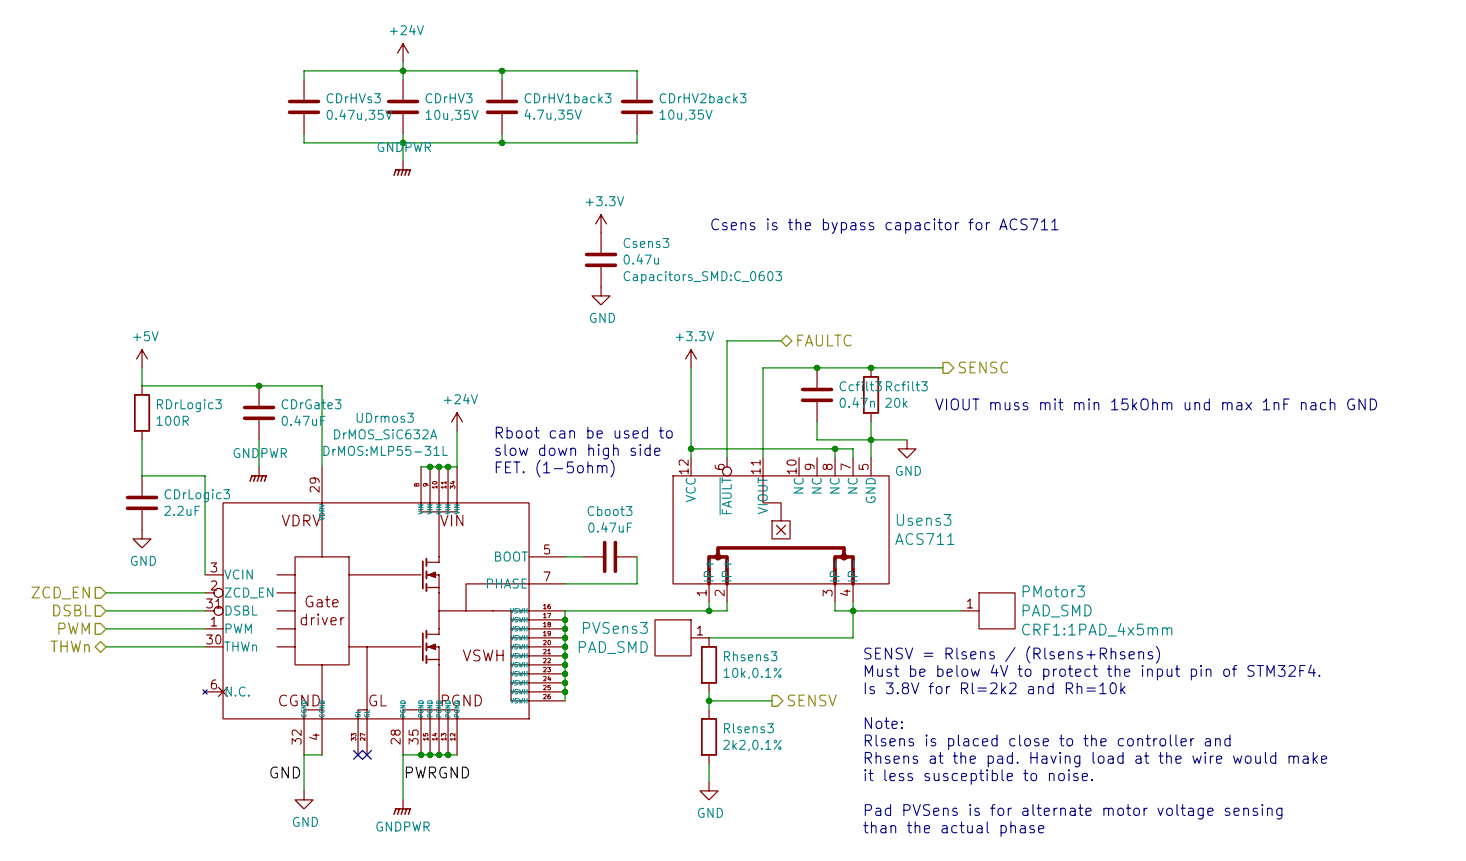
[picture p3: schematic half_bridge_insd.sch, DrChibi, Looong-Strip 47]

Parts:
CDrGate1: 0.47uF; C_0603_HandSoldering
CDrHV1: 10u,35V; C_1206
CDrHV1back1: 4.7u,35V; C_1206
CDrHV2back1: 10u,35V; C_1206_HandSoldering
CDrHVs1: 0.47u,35V; C_0603
CDrLogic1: 2.2uF; C_0603; Part Number C0603C225K8RACTU
Cboot1: 0.47uF; C_0603_HandSoldering
Ccfilt1: 0.47n; C_0402
Csens1: 0.47u; C_0603
PMotor1: PAD_SMD; 1PAD_4x5mm
PVSens1: PAD_SMD; PAD_SMD_1x1
RDrLogic1: 100R; R_0603
Rcfilt1: 20k; R_0402
Rhsens1: 10k,0.1%; C_0603_HandSoldering
Rlsens1: 2k2,0.1%; R_0402
UDrmos1: DrMOS_SiC632A; MLP55-31L; Part Number SiC632ACD-T1-GE3
Usens1: ACS711; QFN-12-1EX_3x3mm_Pitch0.5mm; Part Number ACS711KEXLT-31AB-T

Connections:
+3V3: Csens1.1, Usens1.7 (NC), Usens1.8 (NC), Usens1.12 (VCC); also elsewhere on the board
+5V: CDrGate1.1, RDrLogic1.1, UDrmos1.29 (VDRV); also elsewhere on the board
+24V: CDrHV1.1, CDrHV1back1.1, CDrHV2back1.1, CDrHVs1.1, UDrmos1.8 (VIN), UDrmos1.9 (VIN), UDrmos1.10 (VIN), UDrmos1.11 (VIN), UDrmos1.34 (VIN); also elsewhere on the board
/Half Bridge A/DSBL: UDrmos1.31 (DSBL); also elsewhere on the board
/Half Bridge A/FAULTC: Usens1.6 (~FAULT); also elsewhere on the board
/Half Bridge A/PWM: UDrmos1.1 (PWM); also elsewhere on the board
/Half Bridge A/SENSC: Ccfilt1.1, Rcfilt1.1, Usens1.11 (VIOUT); also elsewhere on the board
/Half Bridge A/THWn: UDrmos1.30 (THWn); also elsewhere on the board
/Half Bridge A/ZCD_EN: UDrmos1.2 (ZCD_EN); also elsewhere on the board
/Virtual Y/SENS1: Rhsens1.2, Rlsens1.1; also elsewhere on the board
GND: CDrGate1.2, CDrHV1.2, CDrHV1back1.2, CDrHV2back1.2, CDrHVs1.2, CDrLogic1.2, Ccfilt1.2, Csens1.2, Rcfilt1.2, Rlsens1.2, UDrmos1.4 (CGND), UDrmos1.12 (PGND), UDrmos1.13 (PGND), UDrmos1.14 (PGND), UDrmos1.15 (PGND), UDrmos1.28 (PGND), UDrmos1.32 (CGND), UDrmos1.35 (PGND), Usens1.5 (GND); also elsewhere on the board
unnamed: CDrLogic1.1, RDrLogic1.2, UDrmos1.3 (VCIN)
unnamed: Cboot1.1, UDrmos1.7 (PHASE)
unnamed: Cboot1.2, UDrmos1.5 (BOOT)
unnamed: PMotor1.1, PVSens1.1, Rhsens1.1, Usens1.3 (IP-), Usens1.4 (IP-)
unnamed: UDrmos1.16 (VSWH), UDrmos1.17 (VSWH), UDrmos1.18 (VSWH), UDrmos1.19 (VSWH), UDrmos1.20 (VSWH), UDrmos1.21 (VSWH), UDrmos1.22 (VSWH), UDrmos1.23 (VSWH), UDrmos1.24 (VSWH), UDrmos1.25 (VSWH), UDrmos1.26 (VSWH), Usens1.1 (IP+), Usens1.2 (IP+)

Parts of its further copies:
C20, C21, C22, C23: 0.47uF; C_0603_HandSoldering
CDrGate2, CDrGate3, CDrGate4, CDrGate5, CDrGate6: 0.47uF; C_0603_HandSoldering
CDrHV1back2, CDrHV1back3, CDrHV1back4, CDrHV1back5, CDrHV1back6: 4.7u,35V; C_1206
CDrHV2, CDrHV3, CDrHV4, CDrHV5, CDrHV6: 10u,35V; C_1206
CDrHV2back2, CDrHV2back3, CDrHV2back4, CDrHV2back5, CDrHV2back6: 10u,35V; C_1206_HandSoldering
CDrHVs2, CDrHVs3, CDrHVs4, CDrHVs5, CDrHVs6: 0.47u,35V; C_0603
CDrLogic2, CDrLogic3, CDrLogic4, CDrLogic5, CDrLogic6: 2.2uF; C_0603; Part Number C0603C225K8RACTU
Cboot2, Cboot3, Cboot4, Cboot5, Cboot6: 0.47uF; C_0603_HandSoldering
Ccfilt2, Ccfilt3, Ccfilt4, Ccfilt5, Ccfilt6: 0.47n; C_0402
Csens2, Csens3, Csens4, Csens5, Csens6: 0.47u; C_0603
PMotor2, PMotor3, PMotor4, PMotor5, PMotor6: PAD_SMD; 1PAD_4x5mm
PVSens2, PVSens3, PVSens4, PVSens5, PVSens6: PAD_SMD; PAD_SMD_1x1
RDrLogic2, RDrLogic3, RDrLogic4, RDrLogic5, RDrLogic6: 100R; R_0603
Rcfilt2, Rcfilt3, Rcfilt4, Rcfilt5, Rcfilt6: 20k; R_0402
Rhsens2, Rhsens3, Rhsens4, Rhsens5, Rhsens6: 10k,0.1%; C_0603_HandSoldering
Rlsens2, Rlsens3, Rlsens4, Rlsens5, Rlsens6: 2k2,0.1%; R_0402
UDrmos2, UDrmos3, UDrmos4, UDrmos5, UDrmos6: DrMOS_SiC632A; MLP55-31L; Part Number SiC632ACD-T1-GE3
Usens2, Usens3, Usens4, Usens5, Usens6: ACS711; QFN-12-1EX_3x3mm_Pitch0.5mm; Part Number ACS711KEXLT-31AB-T

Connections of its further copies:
+3V3: Csens2.1, Csens3.1, Csens4.1, Csens5.1, Csens6.1, Usens2.7 (NC), Usens2.8 (NC), Usens2.12 (VCC), Usens3.7 (NC), Usens3.8 (NC), Usens3.12 (VCC), Usens4.7 (NC), Usens4.8 (NC), Usens4.12 (VCC), Usens5.7 (NC), Usens5.8 (NC), Usens5.12 (VCC), Usens6.7 (NC), Usens6.8 (NC), Usens6.12 (VCC); also elsewhere on the board
+5V: CDrGate2.1, CDrGate3.1, CDrGate4.1, CDrGate5.1, CDrGate6.1, RDrLogic2.1, RDrLogic3.1, RDrLogic4.1, RDrLogic5.1, RDrLogic6.1, UDrmos2.29 (VDRV), UDrmos3.29 (VDRV), UDrmos4.29 (VDRV), UDrmos5.29 (VDRV), UDrmos6.29 (VDRV); also elsewhere on the board
+24V: CDrHV1back2.1, CDrHV1back3.1, CDrHV1back4.1, CDrHV1back5.1, CDrHV1back6.1, CDrHV2.1, CDrHV2back2.1, CDrHV2back3.1, CDrHV2back4.1, CDrHV2back5.1, CDrHV2back6.1, CDrHV3.1, CDrHV4.1, CDrHV5.1, CDrHV6.1, CDrHVs2.1, CDrHVs3.1, CDrHVs4.1, CDrHVs5.1, CDrHVs6.1, UDrmos2.8 (VIN), UDrmos2.9 (VIN), UDrmos2.10 (VIN), UDrmos2.11 (VIN), UDrmos2.34 (VIN), UDrmos3.8 (VIN), UDrmos3.9 (VIN), UDrmos3.10 (VIN), UDrmos3.11 (VIN), UDrmos3.34 (VIN), UDrmos4.8 (VIN), UDrmos4.9 (VIN), UDrmos4.10 (VIN), UDrmos4.11 (VIN), UDrmos4.34 (VIN), UDrmos5.8 (VIN), UDrmos5.9 (VIN), UDrmos5.10 (VIN), UDrmos5.11 (VIN), UDrmos5.34 (VIN), UDrmos6.8 (VIN), UDrmos6.9 (VIN), UDrmos6.10 (VIN), UDrmos6.11 (VIN), UDrmos6.34 (VIN); also elsewhere on the board
/Half Bridge A/FAULTC: Usens2.6 (~FAULT), Usens3.6 (~FAULT), Usens4.6 (~FAULT), Usens5.6 (~FAULT), Usens6.6 (~FAULT); also elsewhere on the board
/Half Bridge A/THWn: UDrmos2.30 (THWn), UDrmos3.30 (THWn), UDrmos4.30 (THWn), UDrmos5.30 (THWn), UDrmos6.30 (THWn); also elsewhere on the board
/Half Bridge A/ZCD_EN: UDrmos2.2 (ZCD_EN), UDrmos3.2 (ZCD_EN), UDrmos4.2 (ZCD_EN), UDrmos5.2 (ZCD_EN), UDrmos6.2 (ZCD_EN); also elsewhere on the board
/Half Bridge B/DSBL: UDrmos2.31 (DSBL); also elsewhere on the board
/Half Bridge B/PWM: UDrmos2.1 (PWM); also elsewhere on the board
/Half Bridge B/SENSC: Ccfilt2.1, Rcfilt2.1, Usens2.11 (VIOUT); also elsewhere on the board
/Half Bridge C/DSBL: UDrmos3.31 (DSBL); also elsewhere on the board
/Half Bridge C/PWM: UDrmos3.1 (PWM); also elsewhere on the board
/Half Bridge C/SENSC: Ccfilt3.1, Rcfilt3.1, Usens3.11 (VIOUT); also elsewhere on the board
/Half Bridge D/DSBL: UDrmos4.31 (DSBL); also elsewhere on the board
/Half Bridge D/PWM: UDrmos4.1 (PWM); also elsewhere on the board
/Half Bridge D/SENSC: Ccfilt4.1, Rcfilt4.1, Usens4.11 (VIOUT); also elsewhere on the board
/Half Bridge E/DSBL: UDrmos5.31 (DSBL); also elsewhere on the board
/Half Bridge E/PWM: UDrmos5.1 (PWM); also elsewhere on the board
/Half Bridge E/SENSC: Ccfilt5.1, Rcfilt5.1, Usens5.11 (VIOUT); also elsewhere on the board
/Half Bridge F/DSBL: UDrmos6.31 (DSBL); also elsewhere on the board
/Half Bridge F/PWM: UDrmos6.1 (PWM); also elsewhere on the board
/Half Bridge F/SENSC: Ccfilt6.1, Rcfilt6.1, Usens6.11 (VIOUT); also elsewhere on the board
/Virtual Y/SENS2: Rhsens2.2, Rlsens2.1; also elsewhere on the board
/Virtual Y/SENS3: Rhsens3.2, Rlsens3.1; also elsewhere on the board
/Virtual Y/SENS4: Rhsens4.2, Rlsens4.1; also elsewhere on the board
/Virtual Y/SENS5: Rhsens5.2, Rlsens5.1; also elsewhere on the board
/Virtual Y/SENS6: Rhsens6.2, Rlsens6.1; also elsewhere on the board
GND: CDrGate2.2, CDrGate3.2, CDrGate4.2, CDrGate5.2, CDrGate6.2, CDrHV1back2.2, CDrHV1back3.2, CDrHV1back4.2, CDrHV1back5.2, CDrHV1back6.2, CDrHV2.2, CDrHV2back2.2, CDrHV2back3.2, CDrHV2back4.2, CDrHV2back5.2, CDrHV2back6.2, CDrHV3.2, CDrHV4.2, CDrHV5.2, CDrHV6.2, CDrHVs2.2, CDrHVs3.2, CDrHVs4.2, CDrHVs5.2, CDrHVs6.2, CDrLogic2.2, CDrLogic3.2, CDrLogic4.2, CDrLogic5.2, CDrLogic6.2, Ccfilt2.2, Ccfilt3.2, Ccfilt4.2, Ccfilt5.2, Ccfilt6.2, Csens2.2, Csens3.2, Csens4.2, Csens5.2, Csens6.2, Rcfilt2.2, Rcfilt3.2, Rcfilt4.2, Rcfilt5.2, Rcfilt6.2, Rlsens2.2, Rlsens3.2, Rlsens4.2, Rlsens5.2, Rlsens6.2, UDrmos2.4 (CGND), UDrmos2.12 (PGND), UDrmos2.13 (PGND), UDrmos2.14 (PGND), UDrmos2.15 (PGND), UDrmos2.28 (PGND), UDrmos2.32 (CGND), UDrmos2.35 (PGND), UDrmos3.4 (CGND), UDrmos3.12 (PGND), UDrmos3.13 (PGND), UDrmos3.14 (PGND), UDrmos3.15 (PGND), UDrmos3.28 (PGND), UDrmos3.32 (CGND), UDrmos3.35 (PGND), UDrmos4.4 (CGND), UDrmos4.12 (PGND), UDrmos4.13 (PGND), UDrmos4.14 (PGND), UDrmos4.15 (PGND), UDrmos4.28 (PGND), UDrmos4.32 (CGND), UDrmos4.35 (PGND), UDrmos5.4 (CGND), UDrmos5.12 (PGND), UDrmos5.13 (PGND), UDrmos5.14 (PGND), UDrmos5.15 (PGND), UDrmos5.28 (PGND), UDrmos5.32 (CGND), UDrmos5.35 (PGND), UDrmos6.4 (CGND), UDrmos6.12 (PGND), UDrmos6.13 (PGND), UDrmos6.14 (PGND), UDrmos6.15 (PGND), UDrmos6.28 (PGND), UDrmos6.32 (CGND), UDrmos6.35 (PGND), Usens2.5 (GND), Usens3.5 (GND), Usens4.5 (GND), Usens5.5 (GND), Usens6.5 (GND); also elsewhere on the board
unnamed: CDrLogic2.1, RDrLogic2.2, UDrmos2.3 (VCIN)
unnamed: CDrLogic3.1, RDrLogic3.2, UDrmos3.3 (VCIN)
unnamed: CDrLogic4.1, RDrLogic4.2, UDrmos4.3 (VCIN)
unnamed: CDrLogic5.1, RDrLogic5.2, UDrmos5.3 (VCIN)
unnamed: CDrLogic6.1, RDrLogic6.2, UDrmos6.3 (VCIN)
unnamed: Cboot2.1, UDrmos2.7 (PHASE)
unnamed: Cboot2.2, UDrmos2.5 (BOOT)
unnamed: Cboot3.1, UDrmos3.7 (PHASE)
unnamed: Cboot3.2, UDrmos3.5 (BOOT)
unnamed: Cboot4.1, UDrmos4.7 (PHASE)
unnamed: Cboot4.2, UDrmos4.5 (BOOT)
unnamed: Cboot5.1, UDrmos5.7 (PHASE)
unnamed: Cboot5.2, UDrmos5.5 (BOOT)
unnamed: Cboot6.1, UDrmos6.7 (PHASE)
unnamed: Cboot6.2, UDrmos6.5 (BOOT)
unnamed: PMotor2.1, PVSens2.1, Rhsens2.1, Usens2.3 (IP-), Usens2.4 (IP-)
unnamed: PMotor3.1, PVSens3.1, Rhsens3.1, Usens3.3 (IP-), Usens3.4 (IP-)
unnamed: PMotor4.1, PVSens4.1, Rhsens4.1, Usens4.3 (IP-), Usens4.4 (IP-)
unnamed: PMotor5.1, PVSens5.1, Rhsens5.1, Usens5.3 (IP-), Usens5.4 (IP-)
unnamed: PMotor6.1, PVSens6.1, Rhsens6.1, Usens6.3 (IP-), Usens6.4 (IP-)
unnamed: UDrmos2.16 (VSWH), UDrmos2.17 (VSWH), UDrmos2.18 (VSWH), UDrmos2.19 (VSWH), UDrmos2.20 (VSWH), UDrmos2.21 (VSWH), UDrmos2.22 (VSWH), UDrmos2.23 (VSWH), UDrmos2.24 (VSWH), UDrmos2.25 (VSWH), UDrmos2.26 (VSWH), Usens2.1 (IP+), Usens2.2 (IP+)
unnamed: UDrmos3.16 (VSWH), UDrmos3.17 (VSWH), UDrmos3.18 (VSWH), UDrmos3.19 (VSWH), UDrmos3.20 (VSWH), UDrmos3.21 (VSWH), UDrmos3.22 (VSWH), UDrmos3.23 (VSWH), UDrmos3.24 (VSWH), UDrmos3.25 (VSWH), UDrmos3.26 (VSWH), Usens3.1 (IP+), Usens3.2 (IP+)
unnamed: UDrmos4.16 (VSWH), UDrmos4.17 (VSWH), UDrmos4.18 (VSWH), UDrmos4.19 (VSWH), UDrmos4.20 (VSWH), UDrmos4.21 (VSWH), UDrmos4.22 (VSWH), UDrmos4.23 (VSWH), UDrmos4.24 (VSWH), UDrmos4.25 (VSWH), UDrmos4.26 (VSWH), Usens4.1 (IP+), Usens4.2 (IP+)
unnamed: UDrmos5.16 (VSWH), UDrmos5.17 (VSWH), UDrmos5.18 (VSWH), UDrmos5.19 (VSWH), UDrmos5.20 (VSWH), UDrmos5.21 (VSWH), UDrmos5.22 (VSWH), UDrmos5.23 (VSWH), UDrmos5.24 (VSWH), UDrmos5.25 (VSWH), UDrmos5.26 (VSWH), Usens5.1 (IP+), Usens5.2 (IP+)
unnamed: UDrmos6.16 (VSWH), UDrmos6.17 (VSWH), UDrmos6.18 (VSWH), UDrmos6.19 (VSWH), UDrmos6.20 (VSWH), UDrmos6.21 (VSWH), UDrmos6.22 (VSWH), UDrmos6.23 (VSWH), UDrmos6.24 (VSWH), UDrmos6.25 (VSWH), UDrmos6.26 (VSWH), Usens6.1 (IP+), Usens6.2 (IP+)

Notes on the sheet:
VIOUT muss mit min 15kOhm und max 1nF nach GND
Rboot can be used to slow down high side FET. (1-5ohm)
SENSV = Rlsens / (Rlsens+Rhsens) Must be below 4V to protect the input pin of STM32F4. Is 3.8V for Rl=2k2 and Rh=10k Note: Rlsens is placed close to the controller and Rhsens at the pad. Having load at the wire would make it less susceptible to noise. Pad PVSens is for alternate motor voltage sensi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
Csens is the bypass capacitor for ACS711

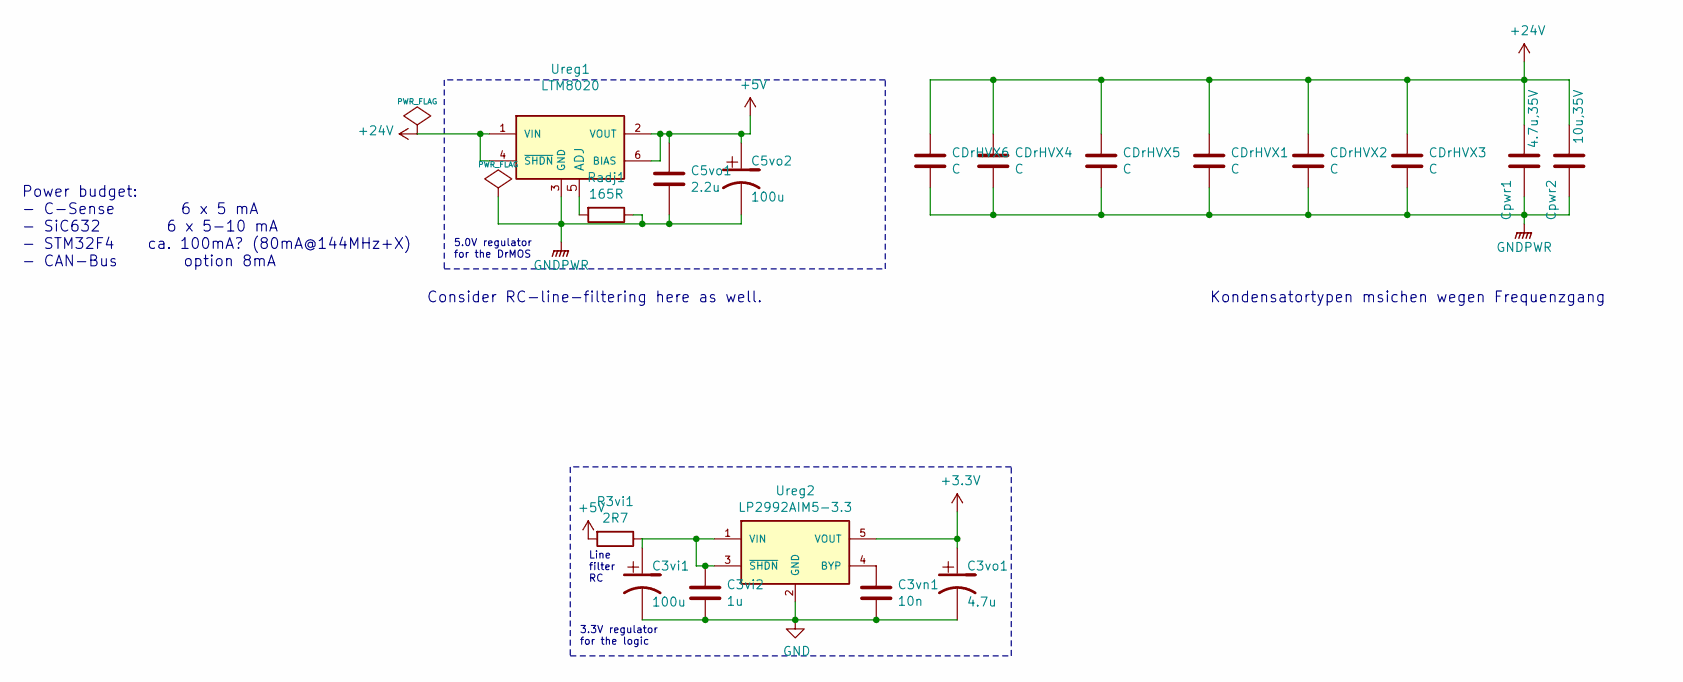
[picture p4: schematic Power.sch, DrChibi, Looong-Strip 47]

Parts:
C3vi1, C5vo2: 100u; C_0805
C3vi2: 1u; C_0603
C3vn1: 10n; C_0603
C3vo1: 4.7u; C_0805
C5vo1: 2.2u; C_0603
CDrHVX1, CDrHVX2, CDrHVX3, CDrHVX4, CDrHVX5, CDrHVX6: C; C_1206
Cpwr1: 4.7u,35V; C_0805
Cpwr2: 10u,35V; C_2220
R3vi1: 2R7; R_0805
Radj1: 165R; R_0402
Ureg1: LTM8020; Housings_LGA_21_6.25x6.25mm; Part Number LTM8020V
Ureg2: LP2992AIM5-3.3; SOT-23-5; Part Number LP2992AIM5-3.3/NOPB

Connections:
+3V3: C3vo1.1, Ureg2.5 (VOUT); also elsewhere on the board
+5V: C5vo1.1, C5vo2.1, R3vi1.2, Ureg1.2 (VOUT), Ureg1.6 (BIAS); also elsewhere on the board
+24V: CDrHVX1.1, CDrHVX2.1, CDrHVX3.1, CDrHVX4.1, CDrHVX5.1, CDrHVX6.1, Cpwr1.2, Cpwr2.2, Ureg1.1 (VIN), Ureg1.4 (~SHDN~); also elsewhere on the board
GND: C3vi1.2, C3vi2.2, C3vn1.2, C3vo1.2, C5vo1.2, C5vo2.2, CDrHVX1.2, CDrHVX2.2, CDrHVX3.2, CDrHVX4.2, CDrHVX5.2, CDrHVX6.2, Cpwr1.1, Cpwr2.1, Radj1.1, Ureg1.3 (GND), Ureg2.2 (GND); also elsewhere on the board
unnamed: C3vi1.1, C3vi2.1, R3vi1.1, Ureg2.1 (VIN), Ureg2.3 (~SHDN~)
unnamed: C3vn1.1, Ureg2.4 (BYP)
unnamed: Radj1.2, Ureg1.5 (ADJ)

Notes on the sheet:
5.0V regulator for the DrMOS
3.3V regulator for the logic
Kondensatortypen msichen wegen Frequenzgang
Line filter RC
Consider RC-line-filtering here as well.
Power budget: - C-Sense 6 x 5 mA - SiC632 6 x 5-10 mA - STM32F4 ca. 100mA? (80mA@144MHz+X) - CAN-Bus option 8mA

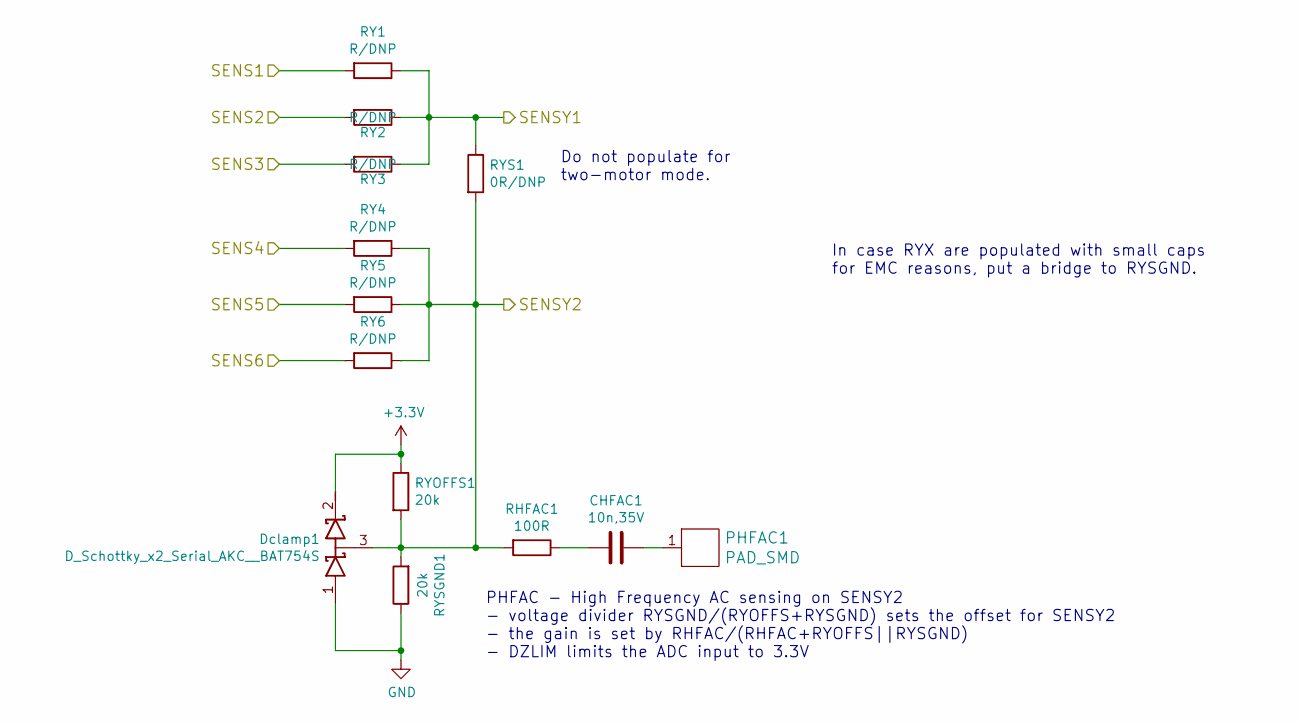
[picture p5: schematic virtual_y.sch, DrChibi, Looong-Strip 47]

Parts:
CHFAC1: 10n,35V; C_0603_HandSoldering
Dclamp1: D_Schottky_x2_Serial_AKC__BAT754S; SOT-23; Part Number BAT754S
PHFAC1: PAD_SMD; PAD_SMD_1.2x2.5
RHFAC1: 100R; R_0603_HandSoldering
RY1, RY2, RY3, RY4, RY5, RY6: R/DNP; R_0603_HandSoldering
RYOFFS1: 20k; R_0603_HandSoldering
RYS1: 0R/DNP; R_0603_HandSoldering
RYSGND1: 20k; R_0402

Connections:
+3V3: Dclamp1.2 (K), RYOFFS1.1; also elsewhere on the board
/MCU/SENSVY1: RY1.1, RY2.1, RY3.1, RYS1.1; also elsewhere on the board
/MCU/SENSVY2: Dclamp1.3 (common), RHFAC1.2, RY4.1, RY5.1, RY6.1, RYOFFS1.2, RYS1.2, RYSGND1.2; also elsewhere on the board
/Virtual Y/SENS1: RY1.2; also elsewhere on the board
/Virtual Y/SENS2: RY2.2; also elsewhere on the board
/Virtual Y/SENS3: RY3.2; also elsewhere on the board
/Virtual Y/SENS4: RY4.2; also elsewhere on the board
/Virtual Y/SENS5: RY5.2; also elsewhere on the board
/Virtual Y/SENS6: RY6.2; also elsewhere on the board
GND: Dclamp1.1 (A), RYSGND1.1; also elsewhere on the board
unnamed: CHFAC1.1, PHFAC1.1
unnamed: CHFAC1.2, RHFAC1.1

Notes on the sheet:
Do not populate for two-motor mode.
In case RYX are populated with small caps for EMC reasons, put a bridge to RYSGND.
PHFAC - High Frequency AC sensing on SENSY2 - voltage divider RYSGND/(RYOFFS+RYSGND) sets the offset for SENSY2 - the gain is set by RHFAC/(RHFAC+RYOFFS||RYSGND) - DZLIM limits the ADC input to 3.3V

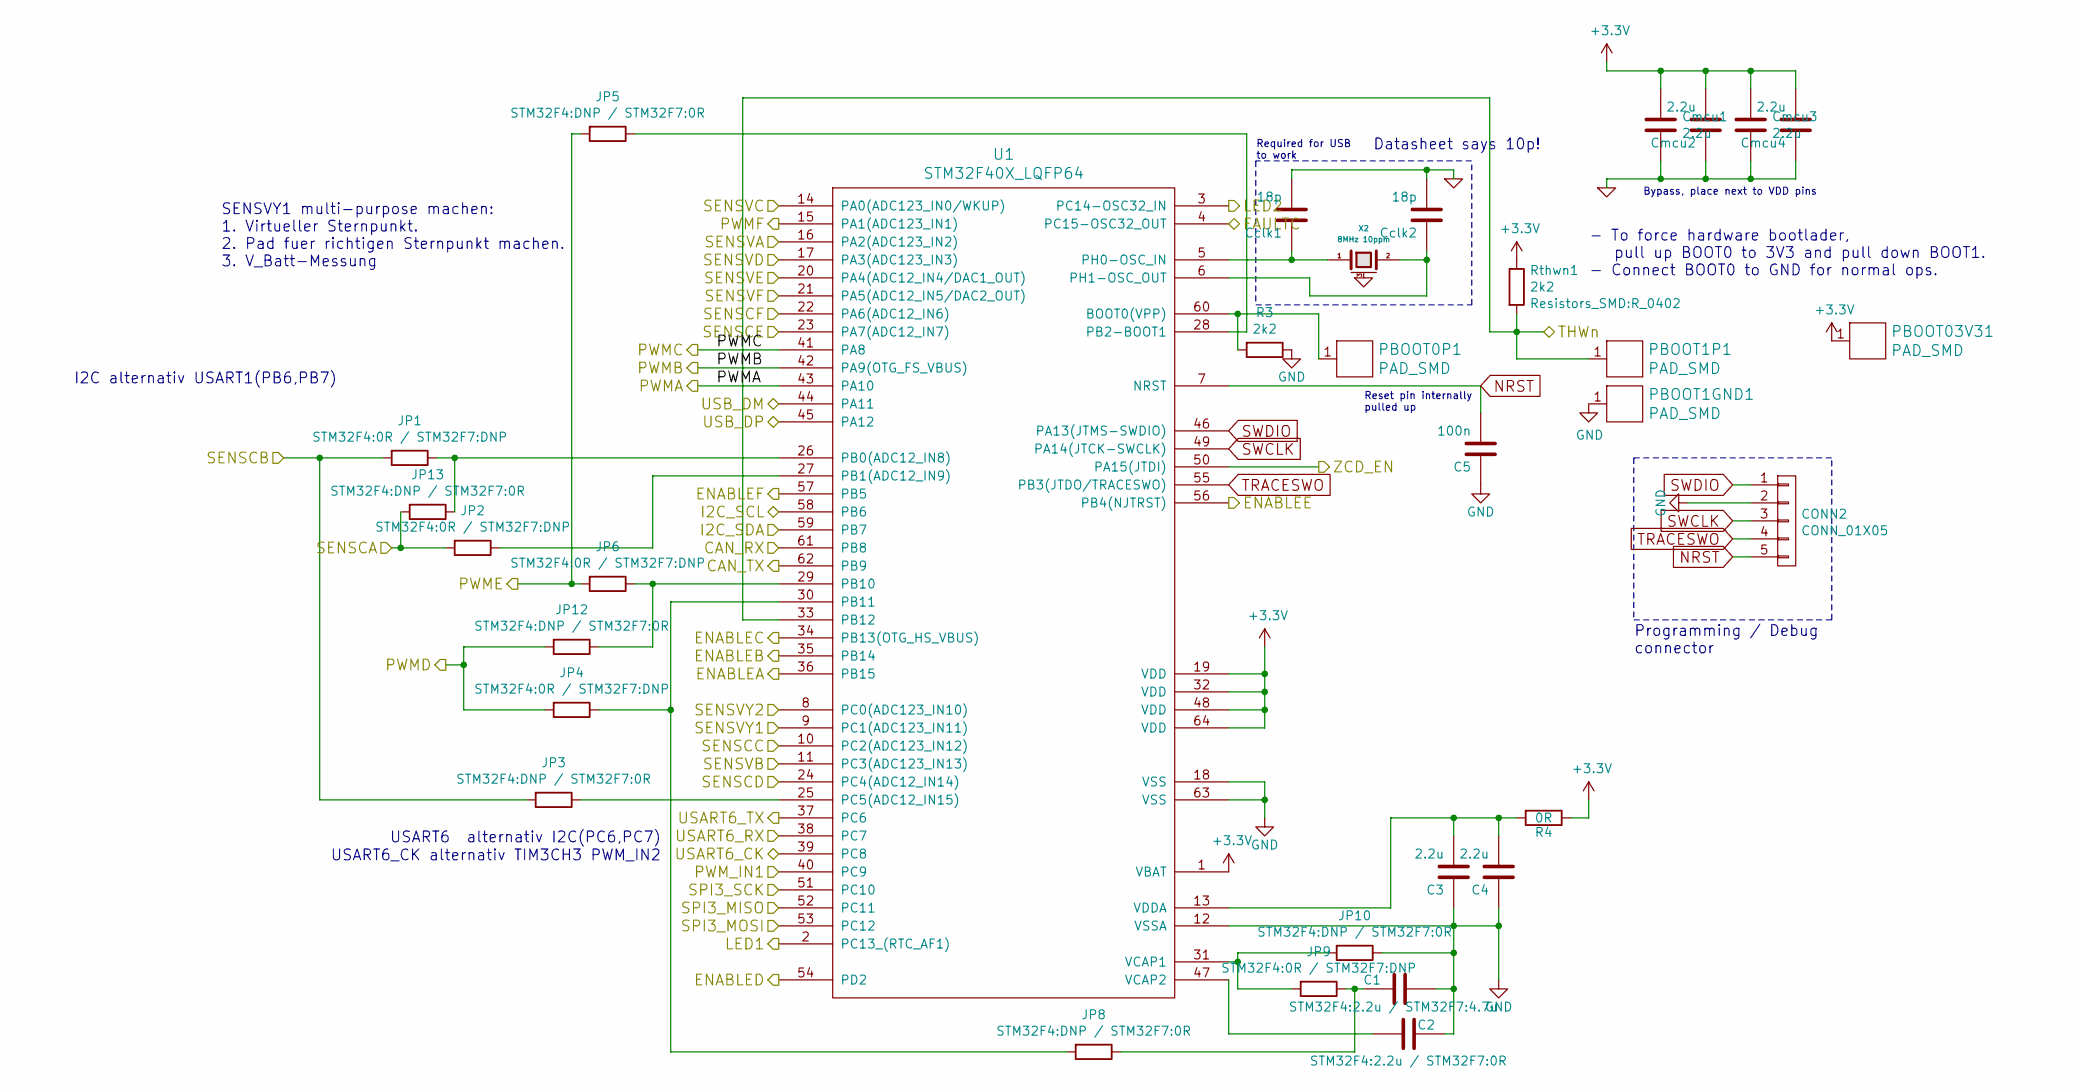
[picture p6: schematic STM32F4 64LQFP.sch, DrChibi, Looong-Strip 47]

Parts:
C1: STM32F4:2.2u / STM32F7:4.7u; C_0603
C2: STM32F4:2.2u / STM32F7:0R; C_0603
C3, C4: 2.2u; C_0603
C5: 100n; C_0603
CONN2: CONN_01X05; Pin_Header_Straight_1x05_Pitch1.27mm
Cclk1, Cclk2: 18p; C_0402
Cmcu1, Cmcu2, Cmcu3, Cmcu4: 2.2u; C_0603
JP1, JP2, JP4, JP6, JP9: STM32F4:0R / STM32F7:DNP; C_0402
JP3, JP5, JP8, JP10, JP12, JP13: STM32F4:DNP / STM32F7:0R; C_0402
PBOOT0P1, PBOOT1GND1, PBOOT1P1, PBOOT03V31: PAD_SMD; PAD_SMD_1x1
R3: 2k2; R_0402
R4: 0R; R_0805
Rthwn1: 2k2; R_0402
U1: STM32F40X_LQFP64; lqfp64_pad_mod; Part Number STM32F405RGTx
X2: 8MHz 10ppm; Crystal_5x3mm; Part Number ABM3B-8.0-10-1UT

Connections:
+3V3: Cmcu1.2, Cmcu2.2, Cmcu3.2, Cmcu4.2, PBOOT03V31.1, R4.1, Rthwn1.1, U1.1 (VBAT), U1.19 (VDD), U1.32 (VDD), U1.48 (VDD), U1.64 (VDD); also elsewhere on the board
/CAN bus transceiver/CAN_RX: U1.61 (PB8); also elsewhere on the board
/CAN bus transceiver/CAN_TX: U1.62 (PB9); also elsewhere on the board
/Half Bridge A/DSBL: U1.36 (PB15); also elsewhere on the board
/Half Bridge A/FAULTC: U1.4 (PC15-OSC32_OUT); also elsewhere on the board
/Half Bridge A/PWM: U1.43 (PA10); also elsewhere on the board
/Half Bridge A/SENSC: JP2.2, JP13.2; also elsewhere on the board
/Half Bridge A/THWn: PBOOT1P1.1, Rthwn1.2, U1.33 (PB12); also elsewhere on the board
/Half Bridge A/ZCD_EN: U1.50 (PA15(JTDI)); also elsewhere on the board
/Half Bridge B/DSBL: U1.35 (PB14); also elsewhere on the board
/Half Bridge B/PWM: U1.42 (PA9(OTG_FS_VBUS)); also elsewhere on the board
/Half Bridge B/SENSC: JP1.2, JP3.2; also elsewhere on the board
/Half Bridge C/DSBL: U1.34 (PB13(OTG_HS_VBUS)); also elsewhere on the board
/Half Bridge C/PWM: U1.41 (PA8); also elsewhere on the board
/Half Bridge C/SENSC: U1.10 (PC2(ADC123_IN12)); also elsewhere on the board
/Half Bridge D/DSBL: U1.54 (PD2); also elsewhere on the board
/Half Bridge D/PWM: JP4.2, JP12.2; also elsewhere on the board
/Half Bridge D/SENSC: U1.24 (PC4(ADC12_IN14)); also elsewhere on the board
/Half Bridge E/DSBL: U1.56 (PB4(NJTRST)); also elsewhere on the board
/Half Bridge E/PWM: JP5.2, JP6.2; also elsewhere on the board
/Half Bridge E/SENSC: U1.23 (PA7(ADC12_IN7)); also elsewhere on the board
/Half Bridge F/DSBL: U1.57 (PB5); also elsewhere on the board
/Half Bridge F/PWM: U1.15 (PA1(ADC123_IN1)); also elsewhere on the board
/Half Bridge F/SENSC: U1.22 (PA6(ADC12_IN6)); also elsewhere on the board
/MCU/I2C_SCL: U1.58 (PB6); also elsewhere on the board
/MCU/I2C_SDA: U1.59 (PB7); also elsewhere on the board
/MCU/LED1: U1.2 (PC13_(RTC_AF1)); also elsewhere on the board
/MCU/LED2: U1.3 (PC14-OSC32_IN); also elsewhere on the board
/MCU/PWM_IN1: U1.40 (PC9); also elsewhere on the board
/MCU/SENSVY1: U1.9 (PC1(ADC123_IN11)); also elsewhere on the board
/MCU/SENSVY2: U1.8 (PC0(ADC123_IN10)); also elsewhere on the board
/MCU/SPI3_MISO: U1.52 (PC11); also elsewhere on the board
/MCU/SPI3_MOSI: U1.53 (PC12); also elsewhere on the board
/MCU/SPI3_SCK: U1.51 (PC10); also elsewhere on the board
/MCU/USART6_CK: U1.39 (PC8); also elsewhere on the board
/MCU/USART6_RX: U1.38 (PC7); also elsewhere on the board
/MCU/USART6_TX: U1.37 (PC6); also elsewhere on the board
/MCU/USB_DM: U1.44 (PA11); also elsewhere on the board
/MCU/USB_DP: U1.45 (PA12); also elsewhere on the board
/Virtual Y/SENS1: U1.16 (PA2(ADC123_IN2)); also elsewhere on the board
/Virtual Y/SENS2: U1.11 (PC3(ADC123_IN13)); also elsewhere on the board
/Virtual Y/SENS3: U1.14 (PA0(ADC123_IN0/WKUP)); also elsewhere on the board
/Virtual Y/SENS4: U1.17 (PA3(ADC123_IN3)); also elsewhere on the board
/Virtual Y/SENS5: U1.20 (PA4(ADC12_IN4/DAC1_OUT)); also elsewhere on the board
/Virtual Y/SENS6: U1.21 (PA5(ADC12_IN5/DAC2_OUT)); also elsewhere on the board
GND: C1.2, C2.2, C3.1, C4.1, C5.1, CONN2.2, Cclk1.2, Cclk2.2, Cmcu1.1, Cmcu2.1, Cmcu3.1, Cmcu4.1, JP10.1, PBOOT1GND1.1, R3.1, U1.12 (VSSA), U1.18 (VSS), U1.63 (VSS), X2.3 (case); also elsewhere on the board
NRST: C5.2, CONN2.5, U1.7 (NRST)
unnamed: C1.1, JP8.1, JP9.1
unnamed: C2.1, U1.47 (VCAP2)
unnamed: C3.2, C4.2, R4.2, U1.13 (VDDA)
unnamed: Cclk1.1, U1.5 (PH0-OSC_IN), X2.1
unnamed: Cclk2.1, U1.6 (PH1-OSC_OUT), X2.2
unnamed: JP1.1, JP13.1, U1.26 (PB0(ADC12_IN8))
unnamed: JP2.1, U1.27 (PB1(ADC12_IN9))
unnamed: JP3.1, U1.25 (PC5(ADC12_IN15))
unnamed: JP4.1, JP8.2, U1.30 (PB11)
unnamed: JP5.1, U1.28 (PB2-BOOT1)
unnamed: JP9.2, JP10.2, U1.31 (VCAP1)
unnamed: JP6.1, JP12.1, U1.29 (PB10)
unnamed: PBOOT0P1.1, R3.2, U1.60 (BOOT0(VPP))
SWCLK: CONN2.3, U1.49 (PA14(JTCK-SWCLK))
SWDIO: CONN2.1, U1.46 (PA13(JTMS-SWDIO))
TRACESWO: CONN2.4, U1.55 (PB3(JTDO/TRACESWO))

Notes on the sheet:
Programming / Debug connector
Reset pin internally pulled up
Required for USB to work
Bypass, place next to VDD pins
SENSVY1 multi-purpose machen: 1. Virtueller Sternpunkt. 2. Pad fuer richtigen Sternpunkt machen. 3. V_Batt-Messung
I2C alternativ USART1(PB6,PB7)
USART6 alternativ I2C(PC6,PC7)
USART6_CK alternativ TIM3CH3 PWM_IN2
Datasheet says 10p!
- To force hardware bootlader, pull up BOOT0 to 3V3 and pull down BOOT1. - Connect BOOT0 to GND for normal ops.

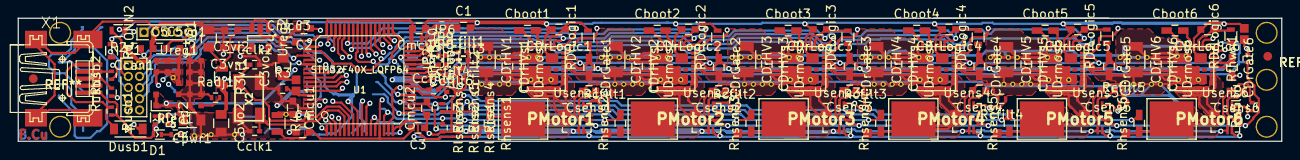
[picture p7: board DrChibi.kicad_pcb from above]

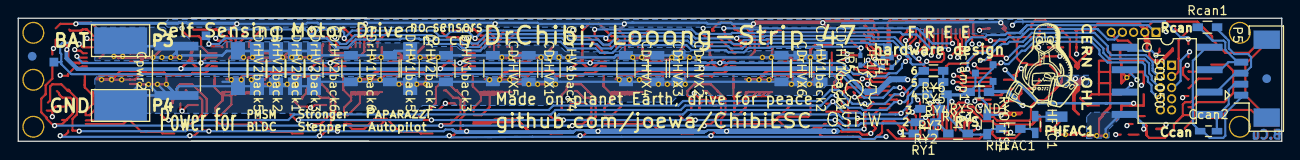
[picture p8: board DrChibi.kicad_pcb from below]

Board: 4 copper layers, 143.5 x 14.0 mm, 188 parts (45 on the bottom side), 111 nets.

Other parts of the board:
REFSYMOSHW: Symbol_OSHW-Logo_SilkScreen

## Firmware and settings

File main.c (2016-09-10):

/*
    ChibiOS - Copyright (C) 2006..2015 Giovanni Di Sirio

    Licensed under the Apache License, Version 2.0 (the "License");
    you may not use this file except in compliance with the License.
    You may obtain a copy of the License at

        http://www.apache.org/licenses/LICENSE-2.0

    Unless required by applicable law or agreed to in writing, software
    distributed under the License is distributed on an "AS IS" BASIS,
    WITHOUT WARRANTIES OR CONDITIONS OF ANY KIND, either express or implied.
    See the License for the specific language governing permissions and
    limitations under the License.
*/

#include "ch.h"
#include "hal.h"
#include "test.h"
#include "chprintf.h"
#include "subsystems/serial/chibiesc_usb.h"
#include <stdint.h>


#define ADC_GRP2_NUM_CHANNELS   2
#define ADC_GRP2_BUF_DEPTH      48

static adcsample_t samples2[ADC_GRP2_NUM_CHANNELS * ADC_GRP2_BUF_DEPTH];


systime_t count_adc, count_frt;
/*
 * ADC streaming callback.
 */
size_t nx = 0, ny = 0;
static void adccallback(ADCDriver *adcp, adcsample_t *buffer, size_t n) {

  (void)adcp;
  if (samples2 == buffer) {
    nx += n;
  }
  else {
    ny += n;
  }
  count_adc++;
}

static void adcerrorcallback(ADCDriver *adcp, adcerror_t err) {

  (void)adcp;
  (void)err;
}


/*
 * ADC conversion group.
 * Mode:        Continuous, 16 samples of 8 channels, SW triggered.
 * Channels:    IN11, IN12, IN11, IN12, IN11, IN12, Sensor, VRef.
 */
static const ADCConversionGroup adcgrpcfg2 = {
  TRUE,
  ADC_GRP2_NUM_CHANNELS,
  adccallback,
  adcerrorcallback,
  0,                        /* CR1 */
  ADC_CR2_SWSTART,          /* CR2 */
  ADC_SMPR1_SMP_AN12(ADC_SAMPLE_3) | ADC_SMPR1_SMP_AN11(ADC_SAMPLE_3),
  0,                        /* SMPR2 */
  ADC_SQR1_NUM_CH(ADC_GRP2_NUM_CHANNELS),
  0,
  ADC_SQR3_SQ2_N(ADC_CHANNEL_IN12)   | ADC_SQR3_SQ1_N(ADC_CHANNEL_IN11)
};



static THD_WORKING_AREA(waThreadFRT, 4096);
static THD_FUNCTION(ThreadFRT, arg) {
	// shortest time to compute, but highest frequency and highest priority
	(void)arg;
	chRegSetThreadName("ThreadFRT");

	int delta_count, last_delta_count;
	delta_count=0; last_delta_count=0;
	count_adc=0; count_frt=0;
	systime_t time = chVTGetSystemTime();
	adcStartConversion(&ADCD1, &adcgrpcfg2, samples2, ADC_GRP2_BUF_DEPTH);

	while (true) {
		time += US2ST(20); //20
		palTogglePad(GPIOD, PIN_LED2);       /* LD3 (orange)  */
		delta_count = count_frt - count_adc;
		if(delta_count != last_delta_count) {
			palTogglePad(GPIOD, PIN_LED1);
		}
		last_delta_count = delta_count;
		count_frt++;
		chThdSleepUntil(time);
		//chThdYield();
	}
}

static THD_WORKING_AREA(waThreadRT, 4096);
static THD_FUNCTION(ThreadRT, arg) {
	// longest time to compute (longer than ThreadFRT frequency, but lower frequency and lowest priority
	// long computation in this thread is interrupted by ThreadFRT and the main loop
	(void)arg;
	chRegSetThreadName("ThreadRT");

	systime_t time = chVTGetSystemTime();

	while (true) {
		time += MS2ST(250);
		int i,i2;
		for (i = 0; i<200000; i++) {
			for (i2 = 0; i2<2; i2++) {
				int a = 5;
				float b = 6.123;
				float c = a / b * i2;
			}
		}
		palTogglePad(GPIOD, PIN_LED3_DISCO);       /* LD6 (blue)  */
		//chThdSleepUntil(time);
		//chThdYield();
    	chThdSleepMilliseconds(100);
	}
}


/*
 * Application entry point.
 */
int main(void) {
	// main loop always runs at NORMALPRIO

  /*
   * System initializations.
   * - HAL initialization, this also initializes the configured device drivers
   *   and performs the board-specific initializations.
   * - Kernel initialization, the main() function becomes a thread and the
   *   RTOS is active.
   */
  halInit();
  chSysInit();

  usb_init(); // Serial over USB initialization


  /*
   * Activates the ADC1 driver and the temperature sensor.
   */
  adcStart(&ADCD1, NULL);
  //adcSTM32EnableTSVREFE();
  /*
   * Starts an ADC continuous conversion.
   */

  chThdCreateStatic(waThreadFRT, sizeof(waThreadFRT), NORMALPRIO+20, ThreadFRT, NULL);
  chThdCreateStatic(waThreadRT, sizeof(waThreadRT), NORMALPRIO-10, ThreadRT, NULL);

  /*
   * Normal main() thread activity, in this demo it does nothing except
   * sleeping in a loop and check the button state.
   */
  while (true) {
    //palTogglePad(GPIOD, PIN_LED1);       /* LD4 (green)  */
	chThdSleepMilliseconds(5);
  }
}

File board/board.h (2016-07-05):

/*
    ChibiOS - Copyright (C) 2006..2015 Giovanni Di Sirio

    Licensed under the Apache License, Version 2.0 (the "License");
    you may not use this file except in compliance with the License.
    You may obtain a copy of the License at

        http://www.apache.org/licenses/LICENSE-2.0

    Unless required by applicable law or agreed to in writing, software
    distributed under the License is distributed on an "AS IS" BASIS,
    WITHOUT WARRANTIES OR CONDITIONS OF ANY KIND, either express or implied.
    See the License for the specific language governing permissions and
    limitations under the License.
*/

#ifndef _BOARD_H_
#define _BOARD_H_

/*
 * Setup for STMicroelectronics STM32F4-Discovery board.
 */

/*
 * Board identifier.
 */
//#define BOARD_ST_STM32F4_DISCOVERY
#define BOARD_DRCHIBI_DISCO
// #define BOARD_NAME                  "STMicroelectronics STM32F4-Discovery"
// #define BOARD_NAME					"BOARD_DRCHIBI"
#define BOARD_NAME					"BOARD_DRCHIBI_DISCO"
/* TODO:
 * Change board identifier to BOARD_DRCHIBI and adapt board name
 */

/*
 * Board oscillators-related settings.
 * NOTE: LSE not fitted.
 */
#if !defined(STM32_LSECLK)
#define STM32_LSECLK                0U
#endif

#if !defined(STM32_HSECLK)
#define STM32_HSECLK                8000000U
#endif

/*
 * Board voltages.
 * Required for performance limits calculation.
 */
#define STM32_VDD                   300U

/*
 * MCU type as defined in the ST header.
 */
#define STM32F407xx
/* TODO:
 * Change to STM32F405xx for DrChibi/ChibiESC
 */

/*
 * IO pins assignments.
 */
#define GPIOA_PIN0                  0U
#define GPIOA_PIN1                  1U
#define GPIOA_PIN2                  2U
#define GPIOA_PIN3                  3U
#define GPIOA_PIN4                  4U
#define GPIOA_PIN5                  5U
#define GPIOA_PIN6                  6U
#define GPIOA_PIN7                  7U
#define GPIOA_PIN8                  8U
#define GPIOA_PIN9                  9U
#define GPIOA_PIN10                 10U
#define GPIOA_PIN11                 11U
#define GPIOA_PIN12                 12U
#define GPIOA_PIN13                 13U
#define GPIOA_PIN14                 14U
#define GPIOA_PIN15                 15U

#define GPIOB_PIN0                  0U
#define GPIOB_PIN1                  1U
#define GPIOB_PIN2                  2U
#define GPIOB_PIN3                  3U
#define GPIOB_PIN4                  4U
#define GPIOB_PIN5                  5U
#define GPIOB_PIN6                  6U
#define GPIOB_PIN7                  7U
#define GPIOB_PIN8                  8U
#define GPIOB_PIN9                  9U
#define GPIOB_PIN10                 10U
#define GPIOB_PIN11                 11U
#define GPIOB_PIN12                 12U
#define GPIOB_PIN13                 13U
#define GPIOB_PIN14                 14U
#define GPIOB_PIN15                 15U

#define GPIOC_PIN0                  0U
#define GPIOC_PIN1                  1U
#define GPIOC_PIN2                  2U
#define GPIOC_PIN3                  3U
#define GPIOC_PIN4                  4U
#define GPIOC_PIN5                  5U
#define GPIOC_PIN6                  6U
#define GPIOC_PIN7                  7U
#define GPIOC_PIN8                  8U
#define GPIOC_PIN9                  9U
#define GPIOC_PIN10                 10U
#define GPIOC_PIN11                 11U
#define GPIOC_PIN12                 12U
#define GPIOC_PIN13                 13U
#define GPIOC_PIN14                 14U
#define GPIOC_PIN15                 15U

#define GPIOD_PIN0                  0U
#define GPIOD_PIN1                  1U
#define GPIOD_PIN2                  2U
#define GPIOD_PIN3                  3U
#define GPIOD_PIN4                  4U
#define GPIOD_PIN5                  5U
#define GPIOD_PIN6                  6U
#define GPIOD_PIN7                  7U
#define GPIOD_PIN8                  8U
#define GPIOD_PIN9                  9U
#define GPIOD_PIN10                 10U
#define GPIOD_PIN11                 11U
#define GPIOD_PIN12                 12U
#define GPIOD_PIN13                 13U
#define GPIOD_PIN14                 14U
#define GPIOD_PIN15                 15U

#define GPIOE_PIN0                  0U
#define GPIOE_PIN1                  1U
#define GPIOE_PIN2                  2U
#define GPIOE_PIN3                  3U
#define GPIOE_PIN4                  4U
#define GPIOE_PIN5                  5U
#define GPIOE_PIN6                  6U
#define GPIOE_PIN7                  7U
#define GPIOE_PIN8                  8U
#define GPIOE_PIN9                  9U
#define GPIOE_PIN10                 10U
#define GPIOE_PIN11                 11U
#define GPIOE_PIN12                 12U
#define GPIOE_PIN13                 13U
#define GPIOE_PIN14                 14U
#define GPIOE_PIN15                 15U
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

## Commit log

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2016-02-07 Created layout for a single DrMOS stage. Need 5 more...
    [CAN.sch, DrChibi.kicad_pcb, DrChibi.sch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]
2016-02-09 Six-phase power stage.
    [CAN.sch, DrChibi.kicad_pcb, DrChibi.sch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]
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2016-02-15 Proceding with layout.
    [DrChibi.kicad_pcb, DrChibi.sch, Power.sch]
2016-02-23 TODO: Routing of the DSBL-signals.
    [CAN.sch, DrChibi.kicad_pcb, DrChibi.sch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]
2016-02-29 TODO: Find appropriate routing to CPU
    [DrChibi.kicad_pcb, DrChibi.sch, Power.sch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]
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2016-03-01 TODO next: Rearrangement and routing of the analog inputs.
    [DrChibi.kicad_pcb, DrChibi.sch, Power.sch]
2016-03-02 Routed all PWM and DSBL
    [DrChibi.kicad_pcb]
2016-03-05 New analog pin configuration for better rounting
    [DrChibi.kicad_pcb, DrChibi.sch, Power.sch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]
2016-03-05 Updated pin config in STM32CubeMX file
    Updated STM32CubeMX file with new ADC inputs according to the PCB layout. Also renamed some pins to be more consistent with schematic and wiki.
2016-03-05 Updated STM32CubeMX file for new ADC configuration
    Updated the STM32CubeMx file to have all phase A-C and Y1 measurements on ADC1 and all phase D-F and Y2 measurements on ADC2.
2016-03-05 Updated STM32CubeMX file with new clock frequencies
    Changed system clock from 168MHz to 144MHz to be able to use maximum ADC frequency of 36MHz.
2016-03-06 Some more routing...
    [CAN.sch, DrChibi.kicad_pcb, DrChibi.sch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]
2016-03-06 Updated STM32CubeMX file with swapped pins
    Swapped PC2 & PC3 (SensVB & V_BAT) and PA15 & PB2 (THWn & Fault_C) according to the new schematics.
2016-03-07 Changed pin for LED3
    [CAN.sch, DrChibi.kicad_pcb, DrChibi.sch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]
2016-03-11 Updated STM32CubeMX file with swapped pins
    Swapped PA15 (Fault_C) with PC15 (LED3) according to the new schematics.
2016-03-11 Next step: connect GND and PWRGND.
    [DrChibi.kicad_pcb, DrChibi.sch, Power.sch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]
2016-03-11 GND and PWRGND connected.
    [DrChibi.kicad_pcb, DrChibi.sch, Power.sch]
2016-03-11 Added some nice logos.
    [DrChibi.kicad_pcb]
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2016-03-12 Fixed DRC problems
    [DrChibi.kicad_pcb]
2016-03-12 Need some mounting holes
    [DrChibi.kicad_pcb]
2016-03-12 Added mounting holes
    [DrChibi.kicad_pcb]
2016-03-12 Fixed solder stop for some pads
    [DrChibi.kicad_pcb]
2016-03-17 Added some part numbers for the BOM
    [DrChibi.sch, Power.sch, STM32F4 64LQFP.sch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]
2016-05-21 Created new component and footprint for regulator LTM8020.
    [DrChibi.sch, Power.sch]
2016-06-08 Fixed numerous typos, syntax errors and omissions for BOARD_DRCHIBI_DISCO config
    [board.h, main.c, mcuconf.h]
2016-06-13 Fixed blinking LED test
    Reconfigured LED pins from open drain to pushpull. Moved LED3 from PA15 to PD15 (so far unused) which is connected to an LED on the Discovery board.
    [board.h, main.c]
2016-06-13 Added the 5V regulator LTM8020 to the schematic.
    [CAN.sch, DrChibi.kicad_pcb, DrChibi.sch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]
2016-06-19 Added basic Serial-over-USB functionality
    - Added "streams" includes to the Makefile in order to be able to use chprintf().
    - Added subsystems/serial/chibiesc_usb.h/.c, configuring an USB CDC device and sending "Test\n" in a loop for testing
    - Including the new usb files and calling usb_init() in main.c
2016-06-30 Removed LED3 to gain some space for the 5V voltage regulator
    [CAN.sch, DrChibi.kicad_pcb, DrChibi.sch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]
2016-07-03 Do DRC check!
    [DrChibi.kicad_pcb, DrChibi.sch, Power.sch]
2016-07-04 Added pullup resistor for THWn. Fixed some not connected parts warnings.
    [DrChibi.kicad_pcb, Power.sch, STM32F4 64LQFP.sch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]
2016-07-05 Updated board config and CubeMX file
    - Removed PIN_LED3 (PA15) from CubeMX file and from board.h for DrChibi.
    - Renamed PIN_LED3 to PIN_LED3_DISCO for the "DrChibi on STM32F4Discovery" in order to keep that LED usable for debugging purpose while avoiding confusion.
    - Swapped PIN_PA15 and PIN_FAULTC in DrChibi board.h config (this wasn't done after the change in schematics and in the wiki).
    - Fixed PIN_VSENS_BAT vs. PIN_VSENS_B mixup and added PIN_EXT for the external analog input pin.
    - Reconfigured all unused pins from input-pullup to input-floating.
    [board.h, main.c]
2016-07-16 Added pullup resistor for THWn.
    [DrChibi.kicad_pcb]
2016-07-16 Guessing current filter values ;-)
    [CAN.sch, DrChibi.sch, Power.sch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]
2016-07-18 Fixed Crystal pin 4 not connected to GND
    [DrChibi.kicad_pcb, Power.sch, STM32F4 64LQFP.sch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]
2016-07-18 Added a few caps on the back next to the DrMOS
    [DrChibi.kicad_pcb, Power.sch, half_bridge_insd.sch]
2016-07-22 For the stencil: the solder mask should be 10% smaller than the pads (for all pads). pcbnew->dimensions->pads mask clearance->solder paste ratio clearance: -10%
    [DrChibi.kicad_pcb]
2016-07-22 Includex 4 fiducials for easier machine setup
    [DrChibi.kicad_pcb]
2016-07-23 Included option for filtering sensev through small caps on RYSx
    [DrChibi.kicad_pcb, STM32F4 64LQFP.sch, virtual_y.sch]
2016-07-25 Fixed footprint CDrHV1back6. Made a few things a little bit nicer.
    [DrChibi.kicad_pcb]
2016-07-26 Added pads PVsensx for the application of alterate voltage sensing probes.
    [CAN.sch, DrChibi.kicad_pcb, DrChibi.sch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]
2016-07-31 Added optional High Frequency AC-coupled voltage sensing port PHFAC
    [DrChibi.kicad_pcb, Power.sch, STM32F4 64LQFP.sch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]
2016-07-31 Added pads for emergency bootloader execution.
    [DrChibi.kicad_pcb, DrChibi.sch, Power.sch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]
2016-08-08 TODO Double-check BOM. Check silk screen. Check Gerber output.
    [DrChibi.kicad_pcb, DrChibi.sch, Power.sch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]
2016-08-09 Added just a few words...
    [DrChibi.kicad_pcb, DrChibi.sch, Power.sch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]
2016-08-17 Updated B.SilkS
    [DrChibi.kicad_pcb]
2016-08-21 STM32F4 overclock configuration that allows maximum ADC clock frequency (288MHz instead of 144MHz; nominal 168MHz)
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2016-09-02 Updated experiment with one very long task that is interrupted by shorter tasks with higher priority.
    [main.c]
2016-09-02 Try to check if frt and adc callback are in sync. Problem: CH_CFG_ST_FREQUENCY works with 60000 but not with higher value?
    [main.c]
2016-09-05 Added "just-in-case-" pads at PWM d,e,f.
    [DrChibi.kicad_pcb, DrChibi.sch, Power.sch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]
2016-09-05 Swapped STM32 Pin33 and Pin50 and added some pads to enable usage of USART3 when TIM8 is bridged to PWM d,e,f.
    [DrChibi.kicad_pcb, DrChibi.sch, Power.sch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]
2016-09-13 Changed statement in B.Silk.
    [DrChibi.kicad_pcb]
2016-10-24 Prepare for fab.
    [CAN.sch, DrChibi-BOM.csv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]
2016-10-25 Little change on B.Silks
    [DrChibi-B.Cu.gbl, DrChibi-B.Mask.gbs, DrChibi-B.Paste.gbp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]
2017-03-20 Renamed hardware design for first revision of Looong-Strip
    [CAN.sch, DrChibi-BOM.csv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]
2017-03-23 Looong-Strip 47!
    [CAN.sch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]
2017-03-30 Fixed drl file and added pick and place data.
    [DrChibi-B.Cu.gbl, DrChibi-B.Fab.gbr, DrChibi-B.Mask.gbs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]
2017-04-01 Fixed little DRC problem.
    [DrChibi-B.Cu.gbl, DrChibi-B.Fab.gbr, DrChibi-B.Mask.gbs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]

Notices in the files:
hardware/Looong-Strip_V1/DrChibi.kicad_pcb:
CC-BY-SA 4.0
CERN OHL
